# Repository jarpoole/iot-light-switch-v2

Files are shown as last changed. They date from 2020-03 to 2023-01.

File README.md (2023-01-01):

# iot-light-switch-v2

An internet-connected voice-controlled easy-to-use lightswitch controller.

## Features

1. Voice control through google-assistant.
2. Extremely long battery life. The wall-mounted lightswitcher can achieve a very low energy sleep state while the base station remains connected to the internet waiting for commmands.
3. Tool-less magnetic installation.
4. Compatibility with both rocker and post style switches.
5. USB rechargable Li-ion battery pack.
6. Side-by-side installation thanks to narrow width.
7. Contact activation through subtle physical switch.

## Limitations

1. The low-energy 433Mhz radios I selected are not suitable for this project as they are extremely unreliable and require a complicated software state-machine to service. A better choice would have been something like the `NRF24L01+` which includes automatic retransmission, multicast and an extremely low power consumption in sleep. See [this](https://github.com/jarpoole/NRF24L01_driver) project for more.

2. The `ESP8266` WiFi module is not powerful enough to act as a base station for multiple devices. Its single processing core is mostly preoccupied with handling the networking stack and cannot be blocked by user software for two long without connectivity problems. A more modern SoC like the `ESP32` would have been a much better choice.

## Subsystems

- [Light Switch](#light-switch)
  - [Motherboard](#motherboard)
  - [Daughterboard](#daughterboard)
  - [Actuator](#actuator)
- [Base Station](#light-switch)

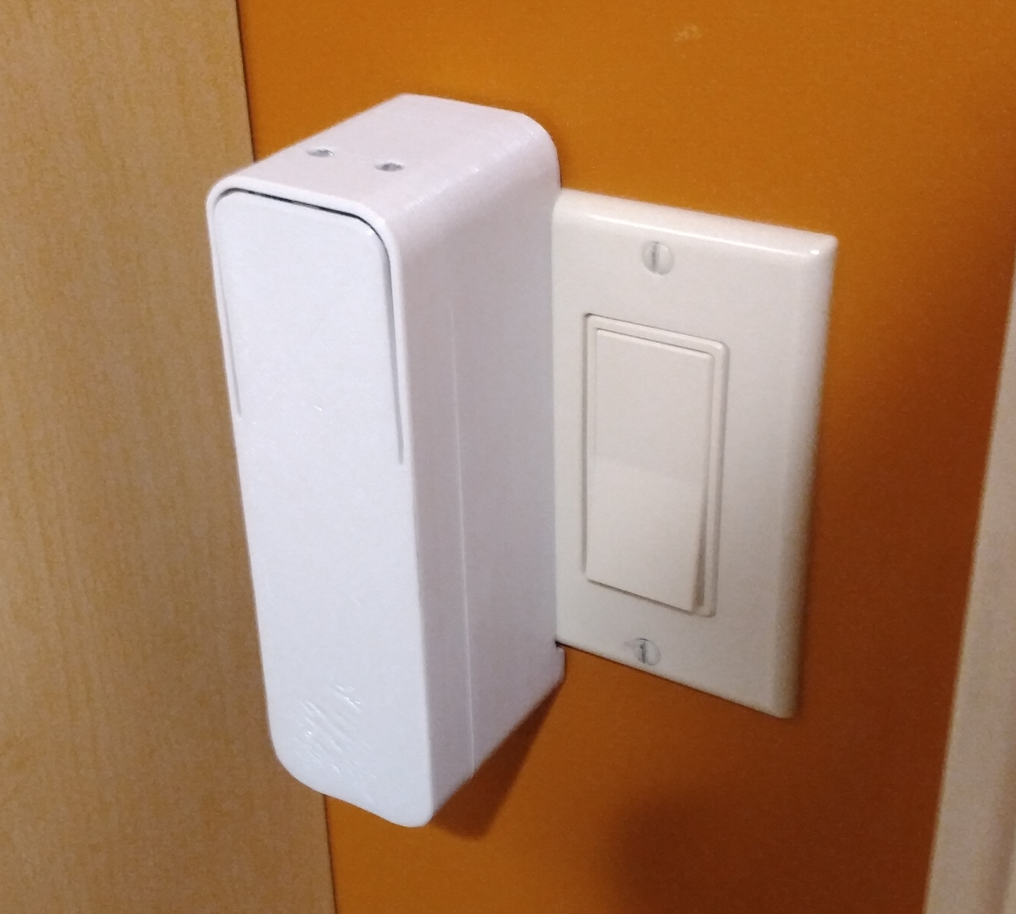
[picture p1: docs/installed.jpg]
installed


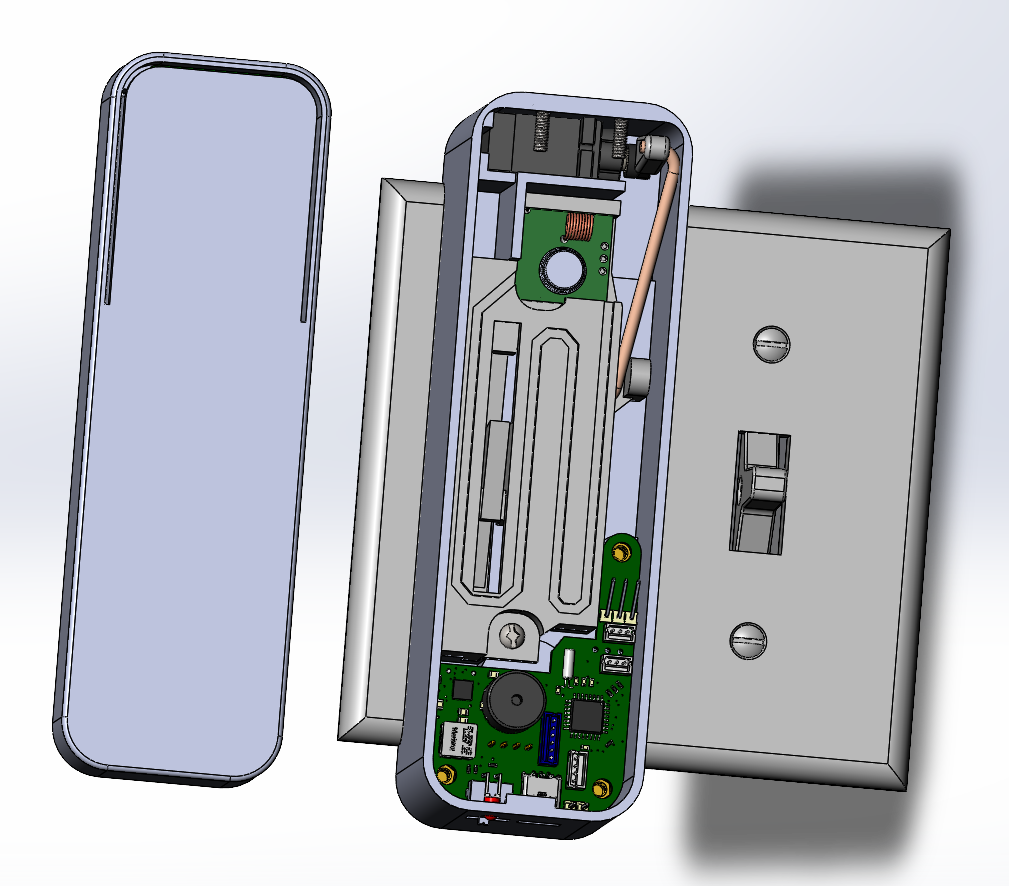
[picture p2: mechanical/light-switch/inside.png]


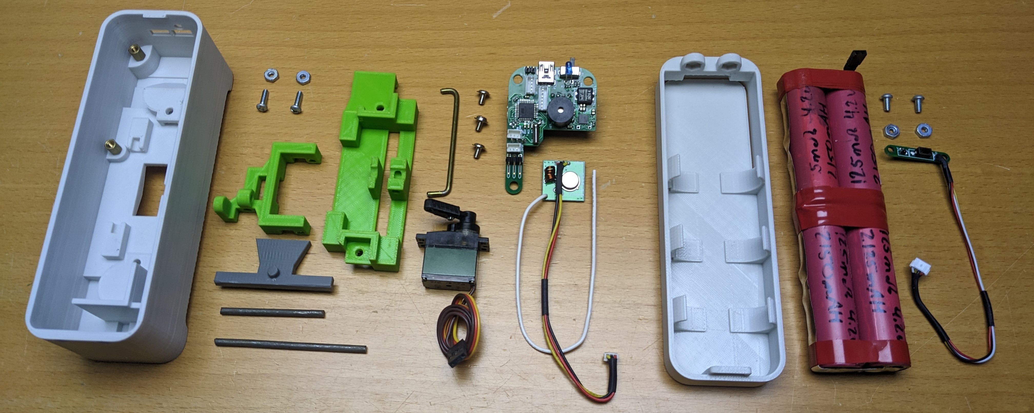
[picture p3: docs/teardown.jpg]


## Light Switch

### Motherboard

1. Low-energy 433Mhz radios
2. Deep-sleep enabled by a 32768Hz oscillator and timer interrupt
3. BMS built around the Texas Instruments BQ25890 buck-boost charge controller. Charges 3.7 Li-ion battery pack from 5v USB power (buck) and produces 5v system power from battery pack when in operation (boost)
4. Audio feedback from a buzzer
5. Integrated USB debug/serial output
6. ICSP programming header

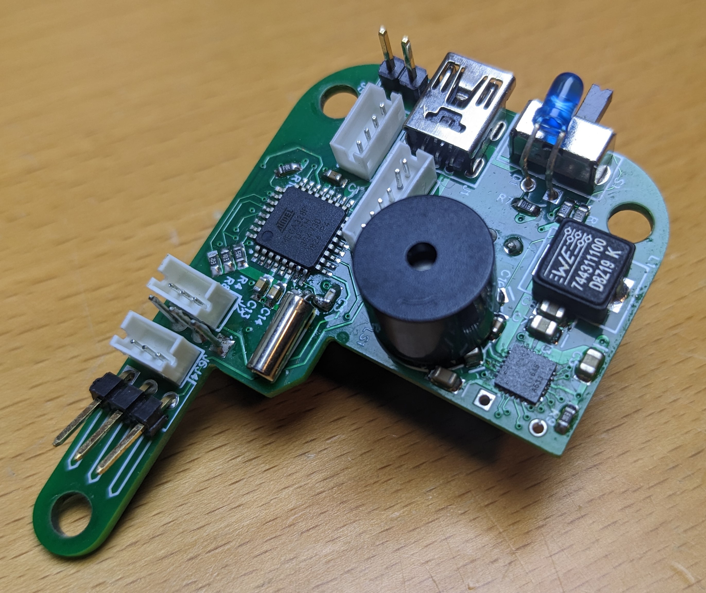
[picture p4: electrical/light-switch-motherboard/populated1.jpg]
motherboard_populated


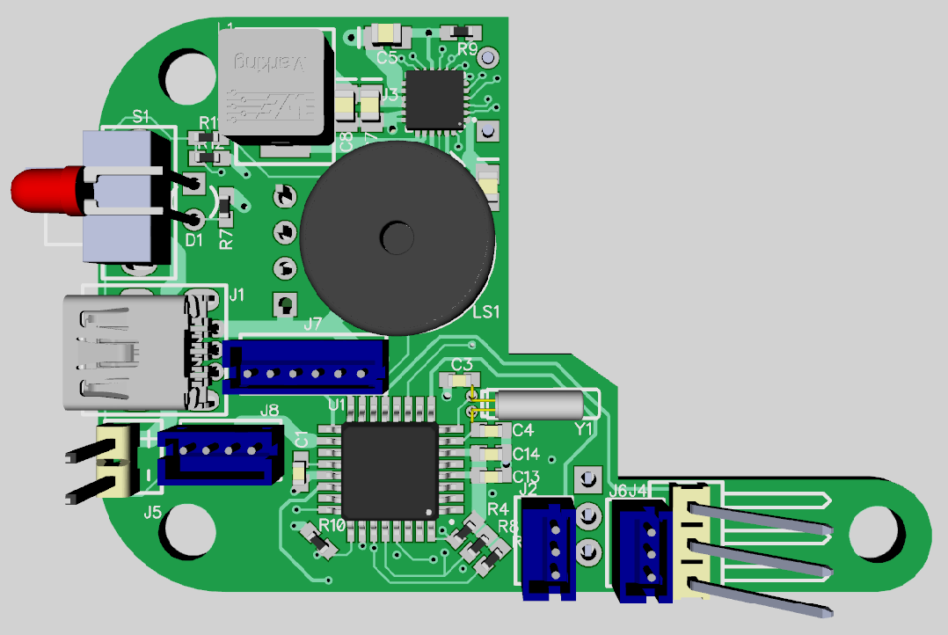
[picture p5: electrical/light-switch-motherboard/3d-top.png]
motherboard_3d_top


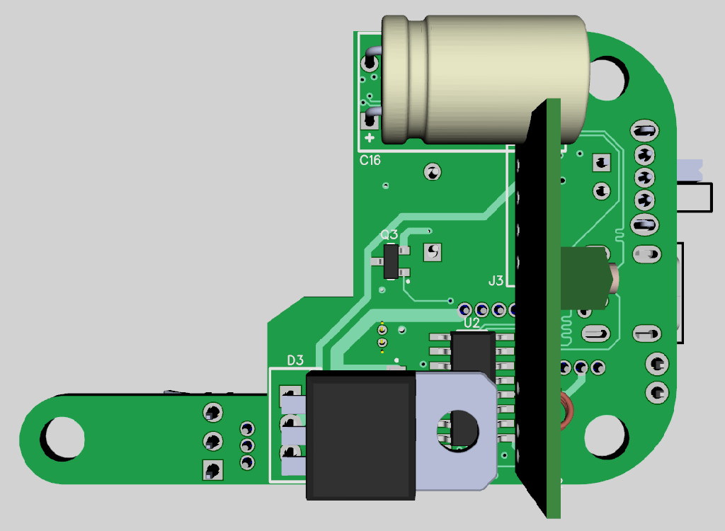
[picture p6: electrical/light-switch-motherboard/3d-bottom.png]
motherboard_3d_bottom


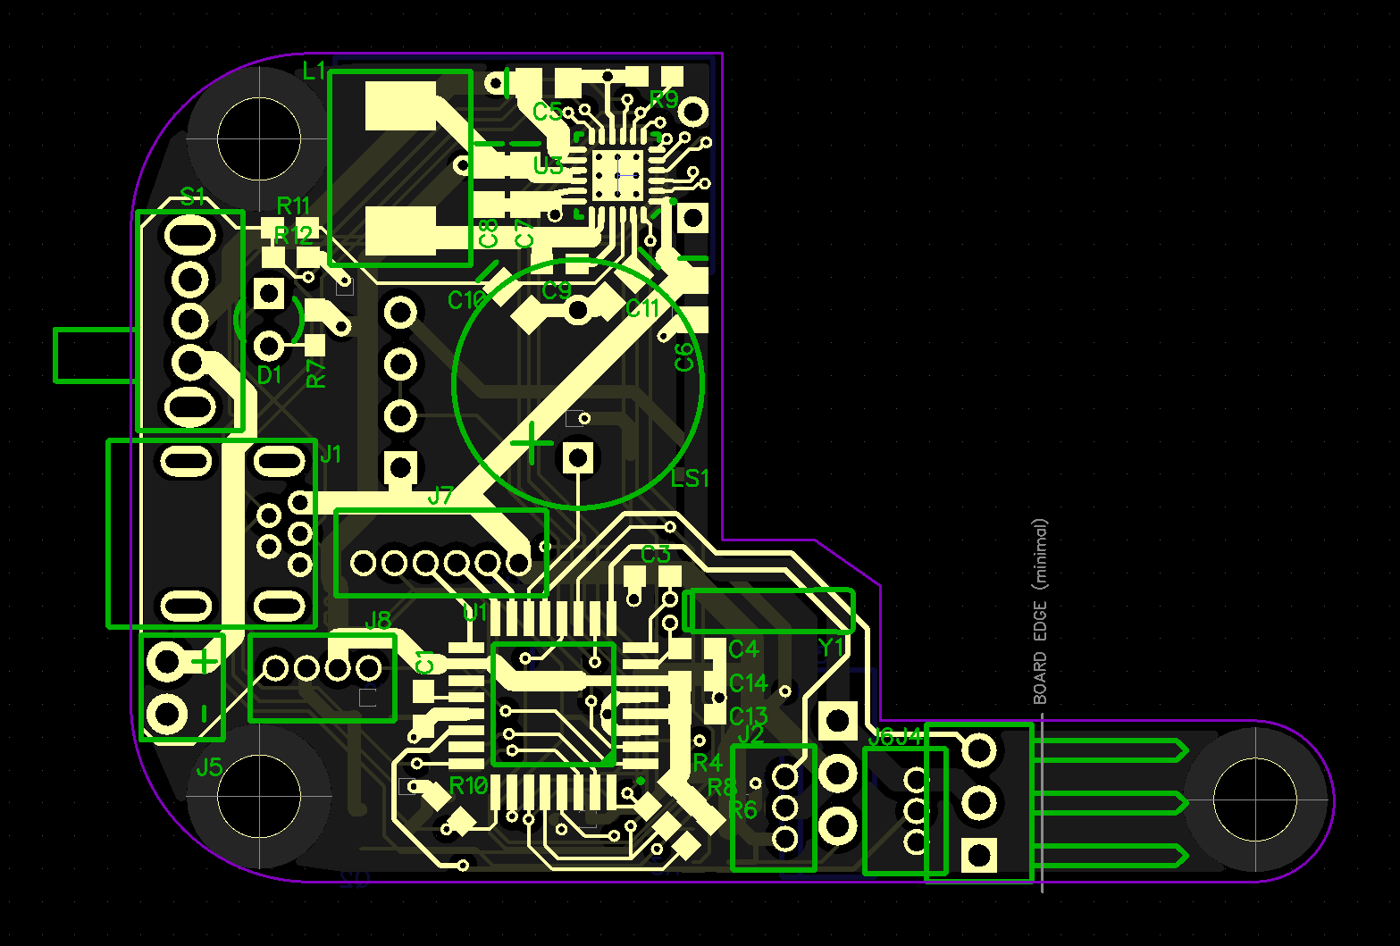
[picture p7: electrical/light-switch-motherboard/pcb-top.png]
motherboard_pcb_top


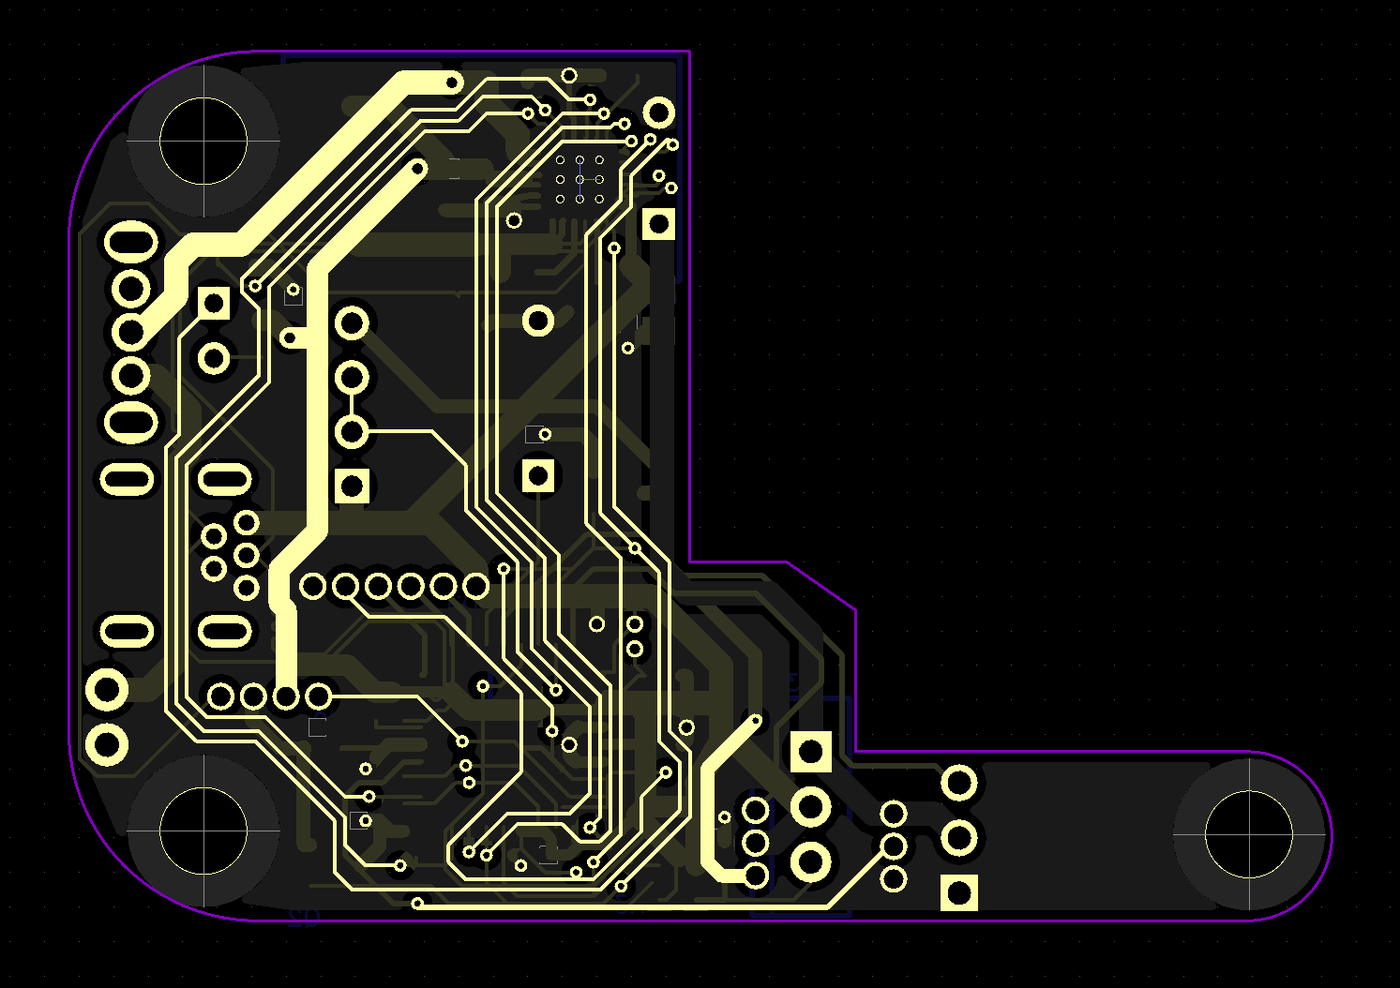
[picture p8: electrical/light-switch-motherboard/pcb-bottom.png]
motherboard_pcb_bottom


### Daughterboard

The daughterboard has two roles

1. To connect a small momentary switch for the front bumper to the motherboard
2. To connect the battery temperature monitoring thermocouple to the motherboard

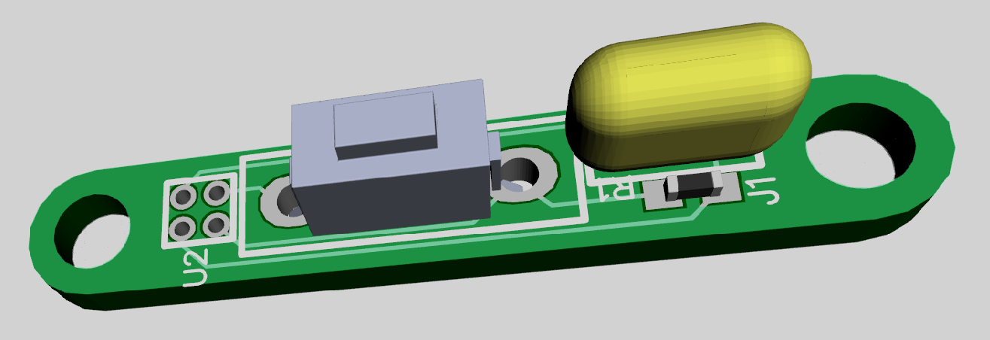
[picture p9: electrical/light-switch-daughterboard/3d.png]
daughterboard_3d


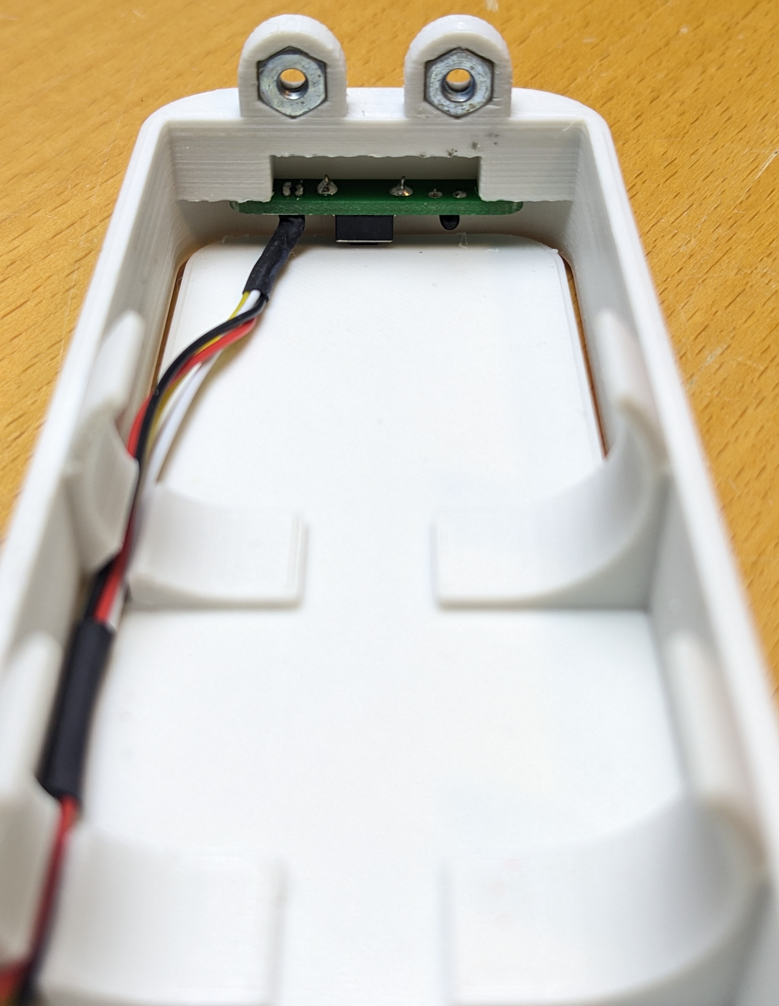
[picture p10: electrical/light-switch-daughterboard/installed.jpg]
daughterboard_installed


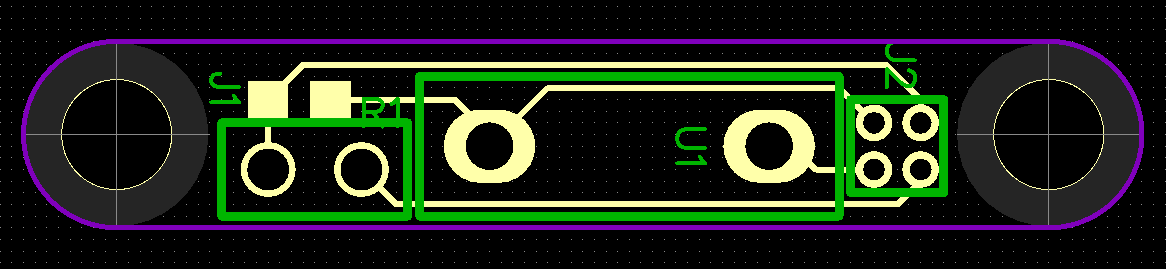
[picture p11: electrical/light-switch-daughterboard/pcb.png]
daughterboard_pcb


### Actuator

The actuator is compatible with both post-style and rocker-style switches. The slide engages with post-style while the vertial rocker engages the rocker-style.

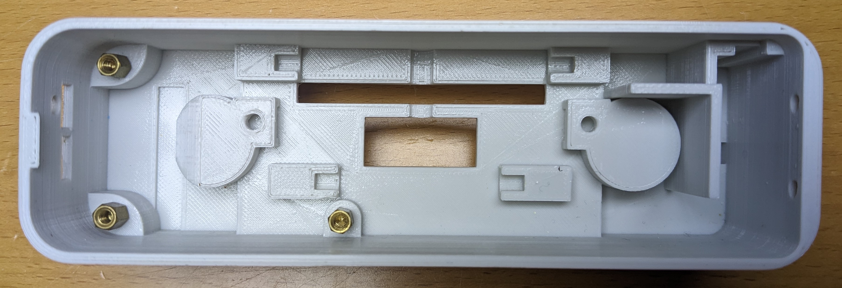
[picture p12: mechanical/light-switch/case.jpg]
case


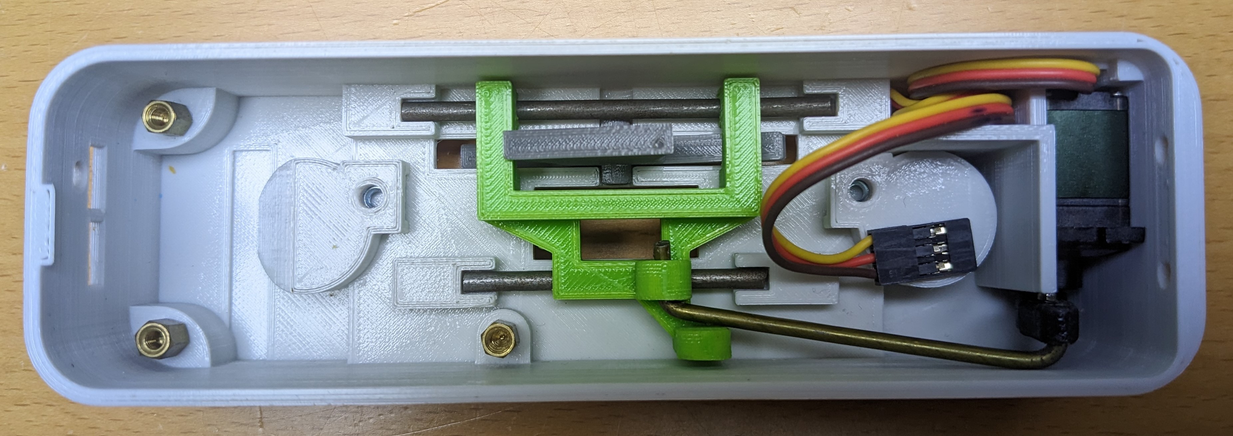
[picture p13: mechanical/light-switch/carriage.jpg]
carriage


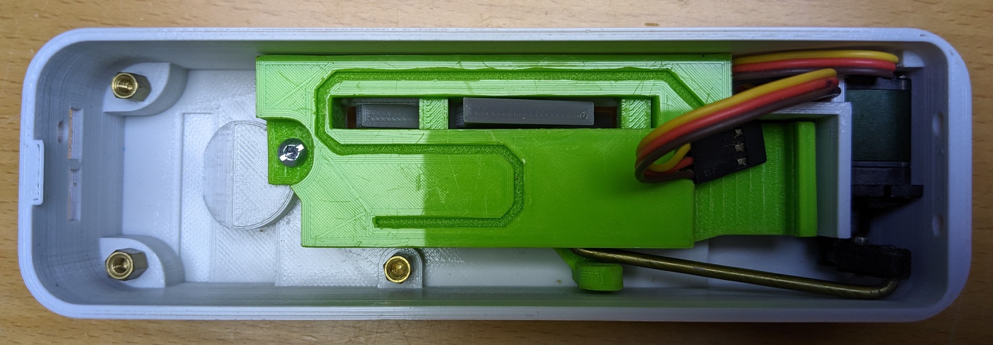
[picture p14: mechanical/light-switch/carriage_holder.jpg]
carriage_holder


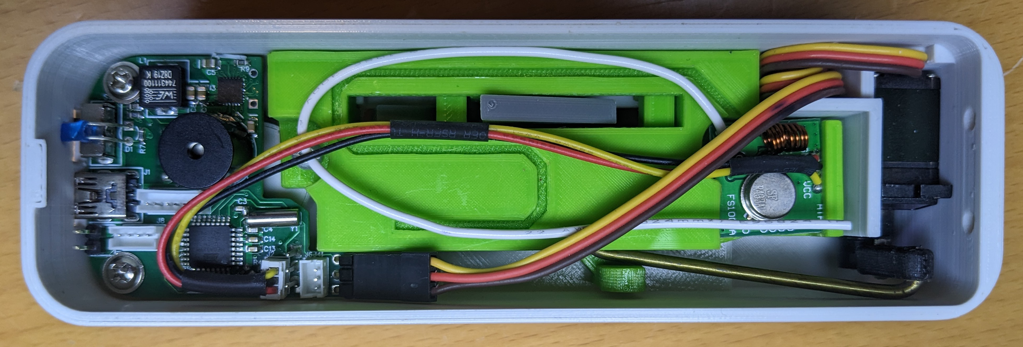
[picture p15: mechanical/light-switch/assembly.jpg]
assembled


## Base Station

The base station's primary responsibility is to act as a bridge between the internet and the low-energy 433Mhz radio on the light-switch.

1. WiFi connectivity using ESP8266
2. Dual power-supply options
   - Mini USB
   - Terminal block 5V DC
3. Integrated USB debug/serial output
4. Captive portal configuration through a mobile browser

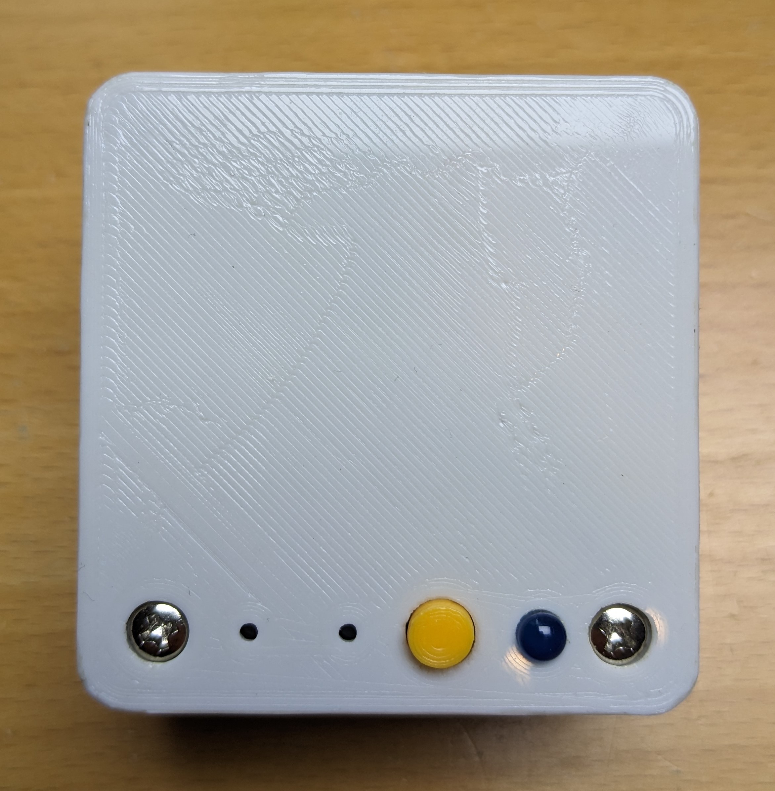
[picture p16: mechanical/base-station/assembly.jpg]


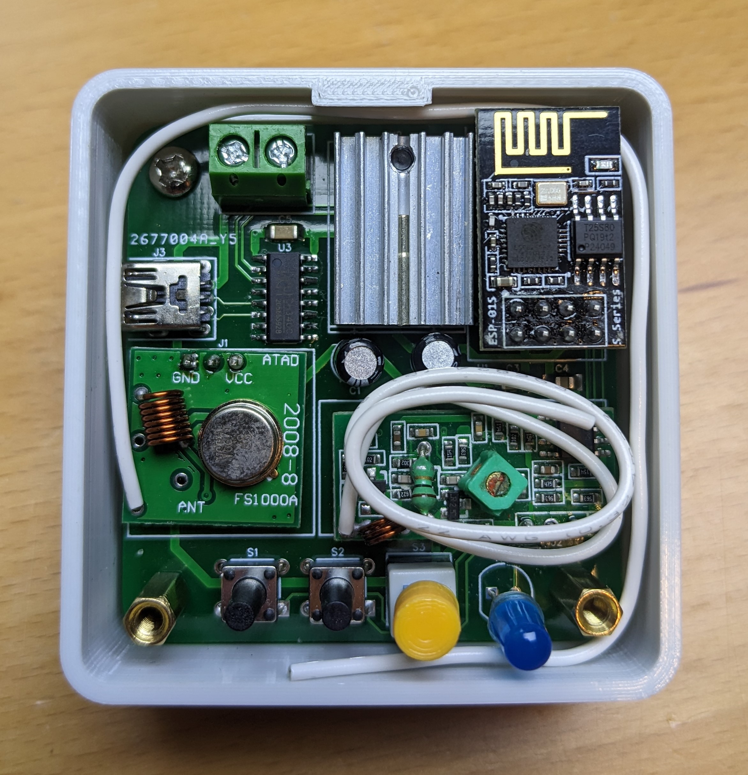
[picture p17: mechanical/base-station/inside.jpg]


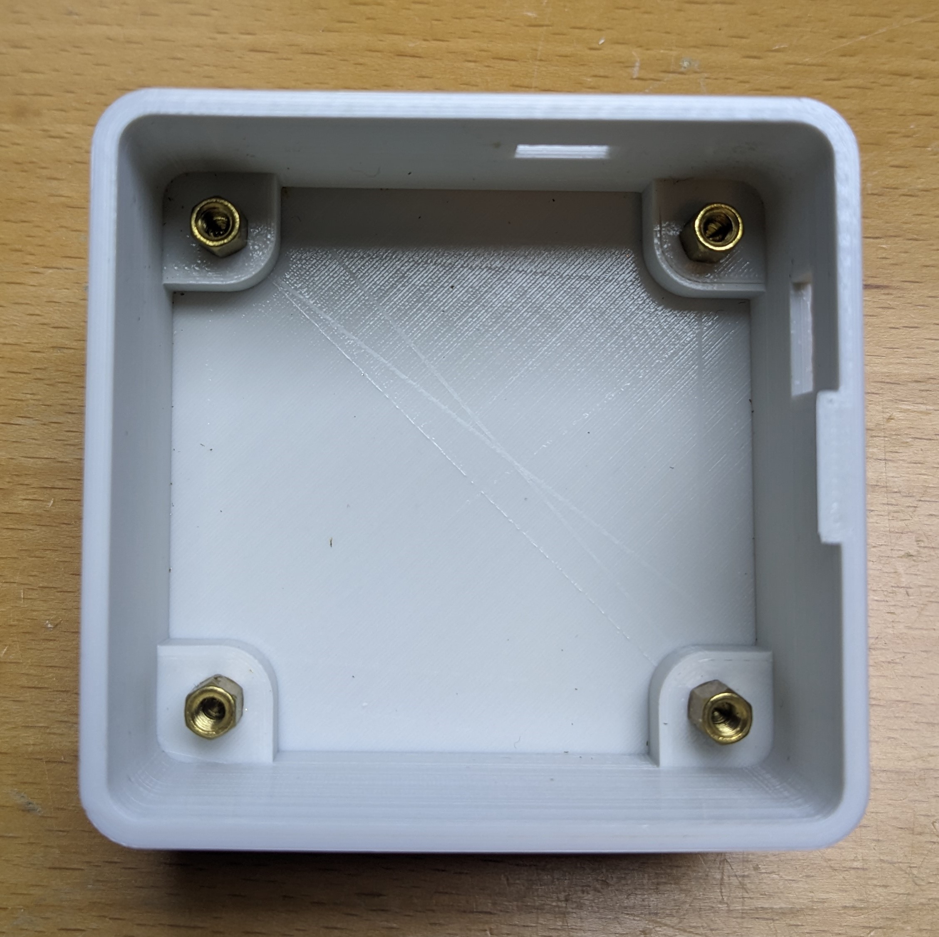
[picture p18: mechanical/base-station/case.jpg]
case


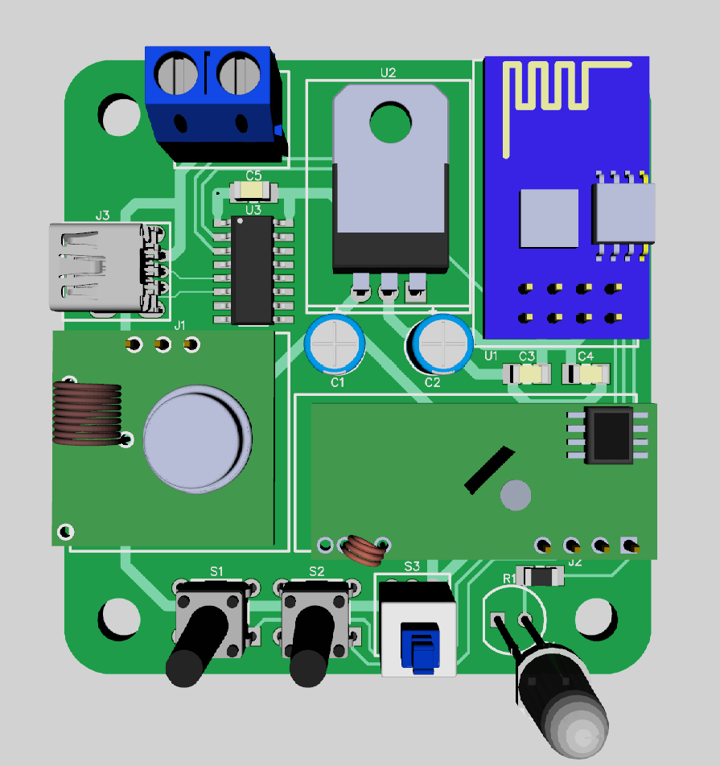
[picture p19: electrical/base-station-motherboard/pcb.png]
base_pcb


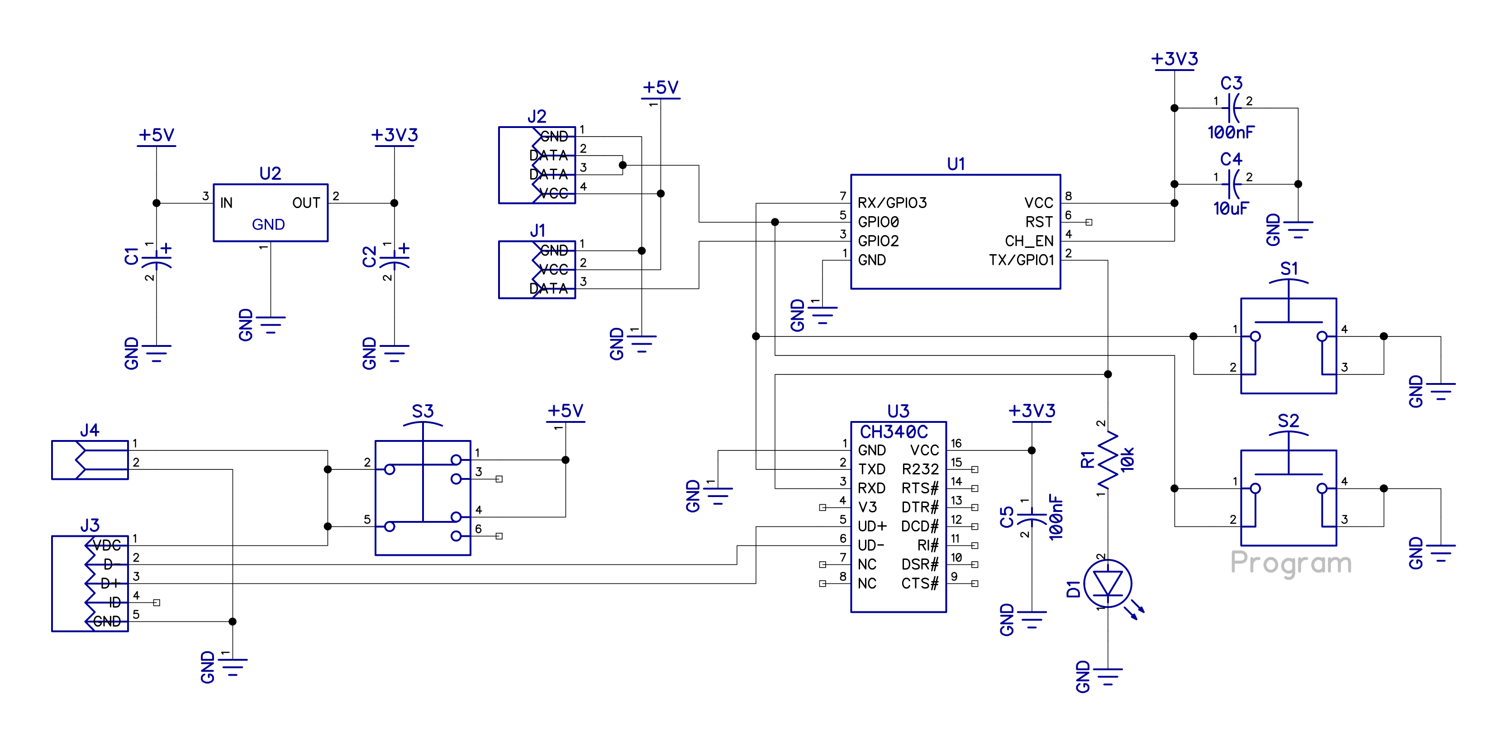
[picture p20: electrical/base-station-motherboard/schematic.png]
schematic


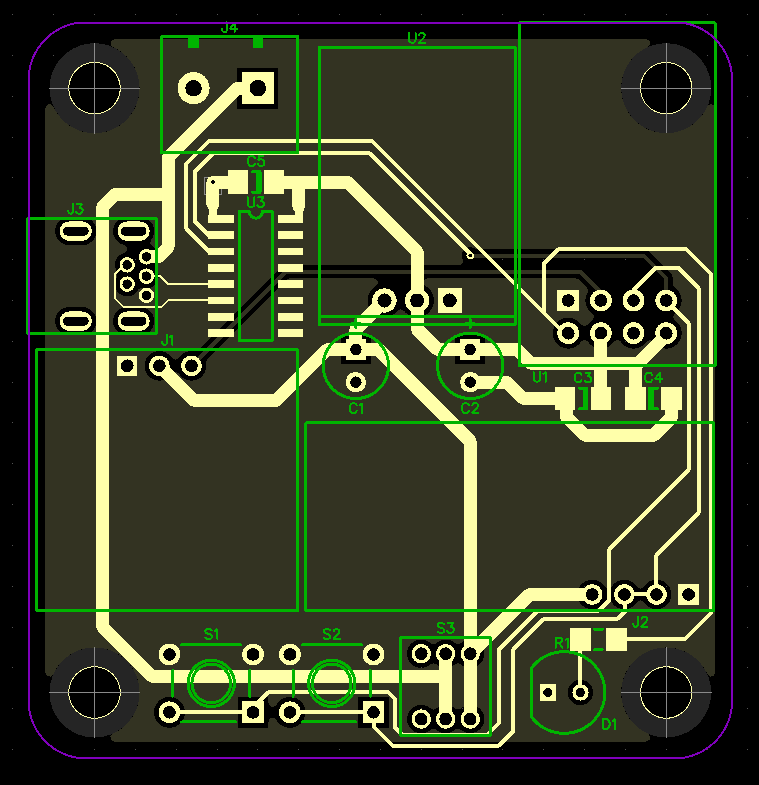
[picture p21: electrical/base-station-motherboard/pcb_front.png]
base_pcb


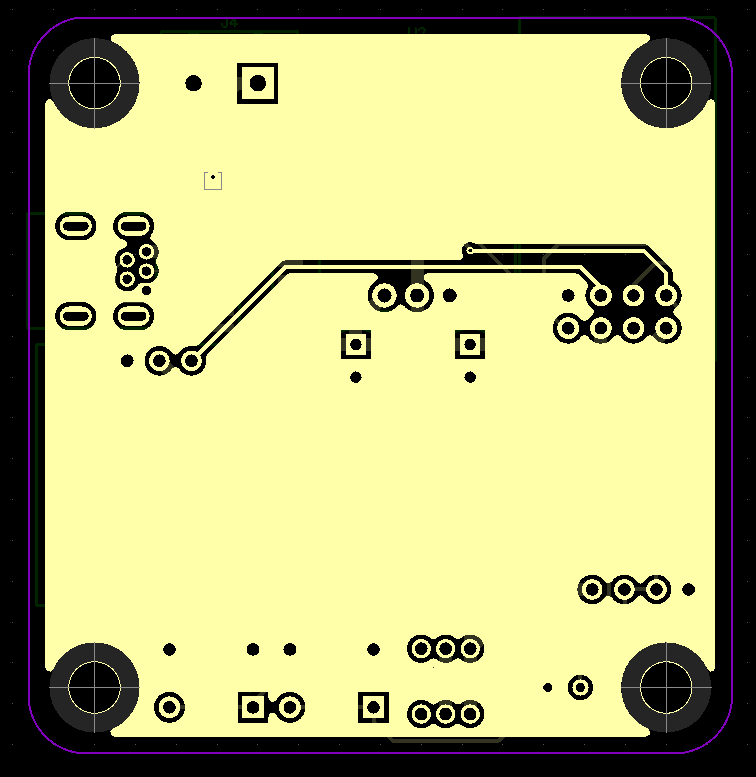
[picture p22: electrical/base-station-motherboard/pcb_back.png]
base_pcb


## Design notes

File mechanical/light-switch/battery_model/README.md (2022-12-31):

# 1s4p 18650 Battery Pack

## Render

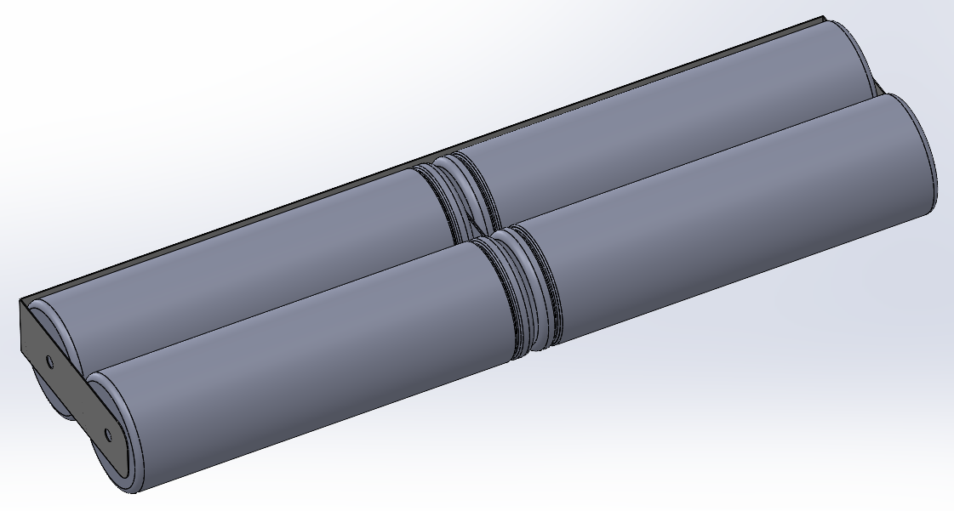
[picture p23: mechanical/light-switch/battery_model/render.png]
render


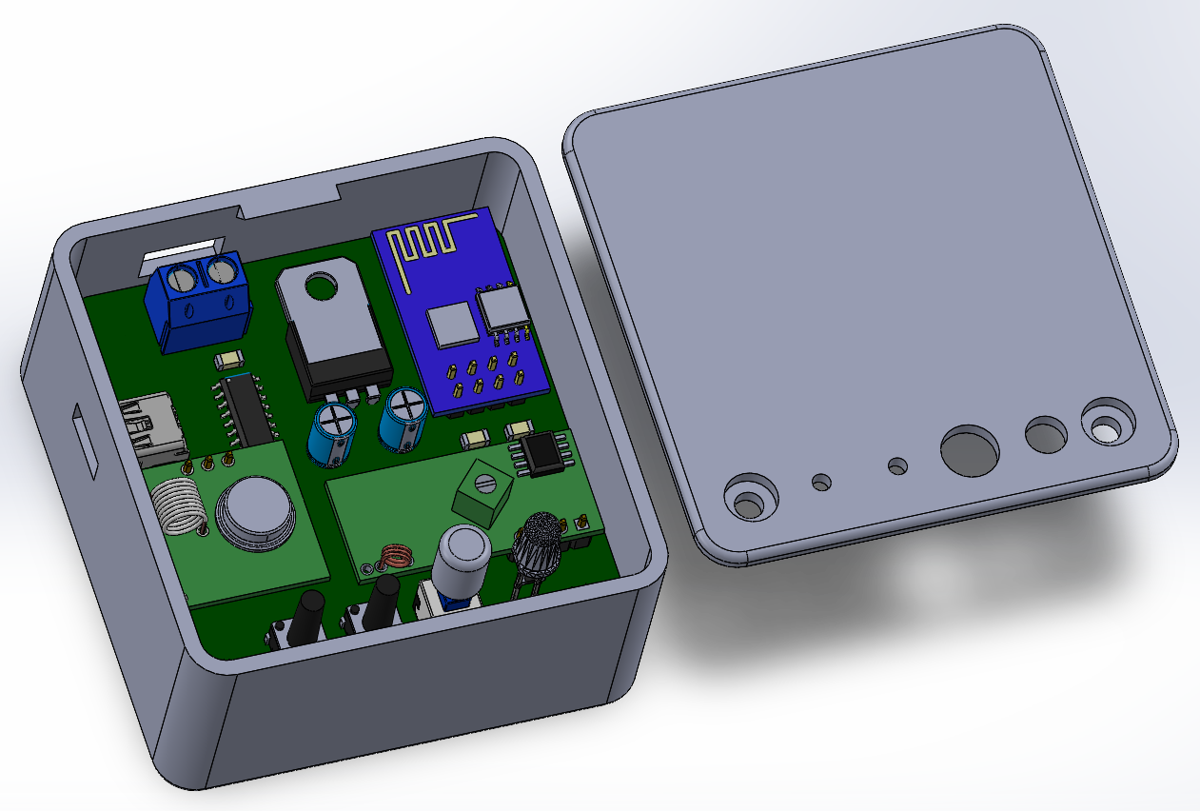
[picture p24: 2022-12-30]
mechanical/base-station/render.png

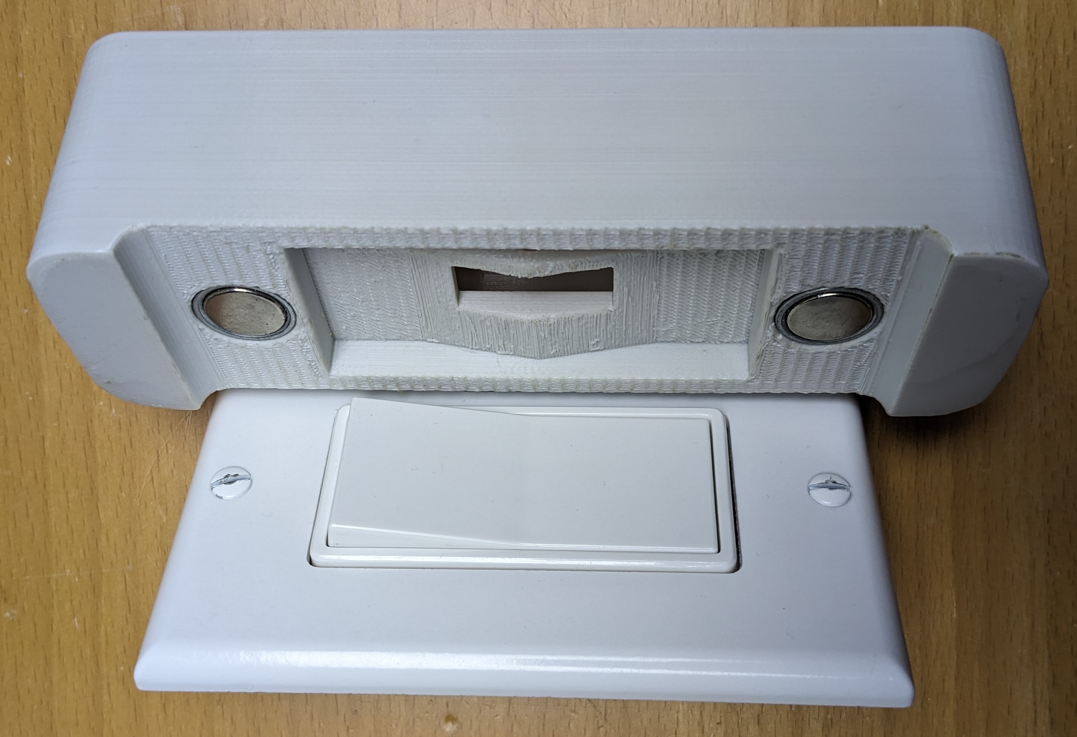
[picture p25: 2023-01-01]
mechanical/light-switch/mount.jpg

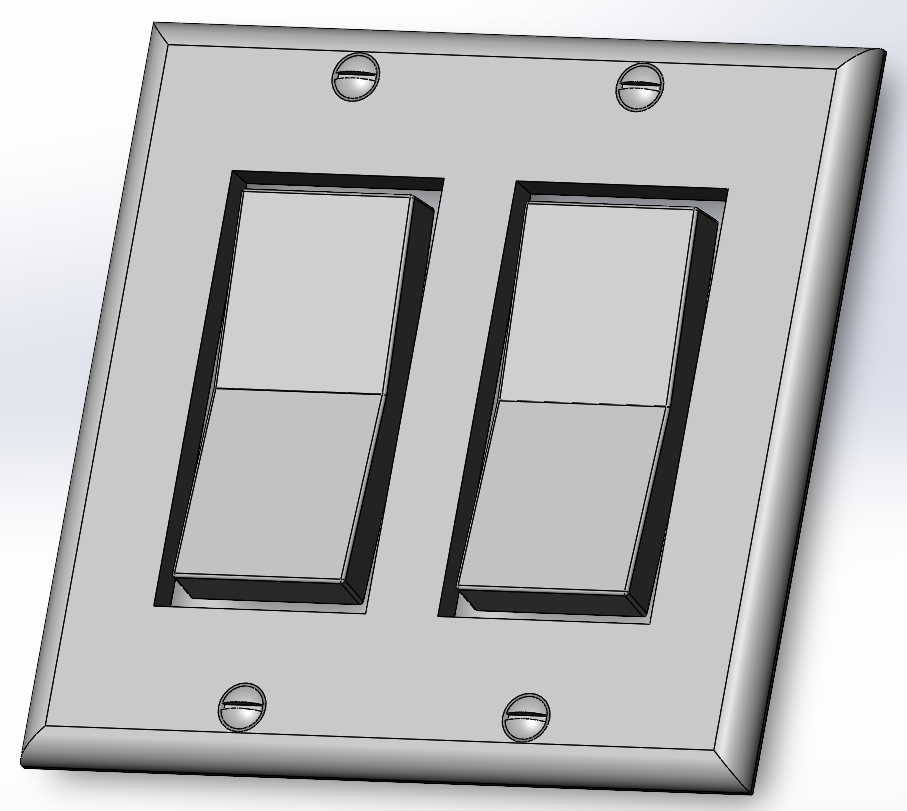
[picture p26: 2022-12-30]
mechanical/light-switch/rocker-switch-model/render.png

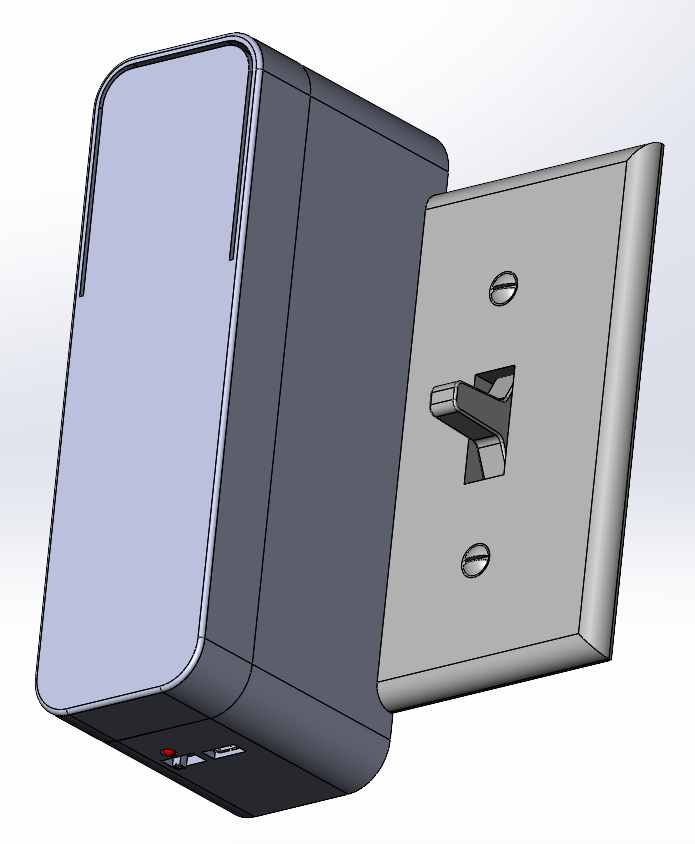
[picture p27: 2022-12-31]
mechanical/light-switch/render.png

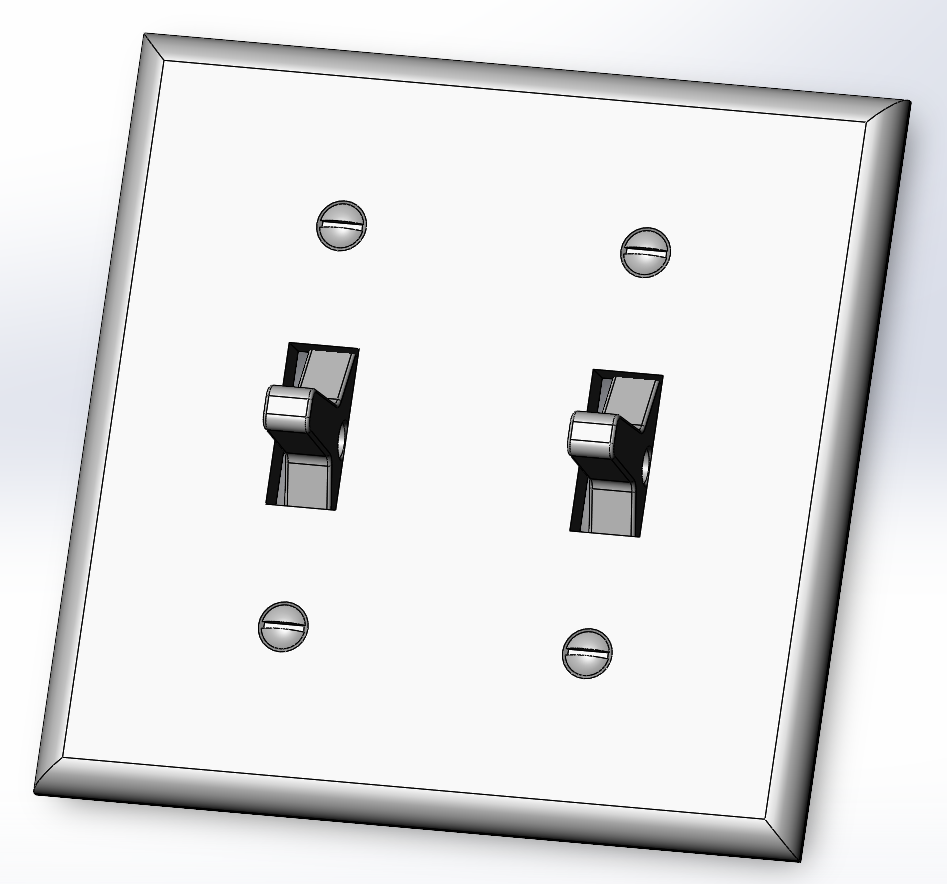
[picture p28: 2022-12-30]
mechanical/light-switch/post-switch-model/render.png

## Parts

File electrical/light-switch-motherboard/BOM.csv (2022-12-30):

Name | Quantity | RefDef | Value
CAP_0603 | 2 | C3, C4 | 18pF
CAP_0603 | 1 | C9 | 47nF
CAP_0603 | 1 | C12 | 10nF
CAP_0603 | 4 | C1, C13, C14, C15 | 100nF
CAP_0805 | 1 | C10 | 4.7uF
CAP_0805 | 4 | C5, C7, C8, C11 | 10uF
CAP_0805 | 1 | C6 | 1uF
CAP Radial Right Angle 10x16x5 | 1 | C16 | 1000uF
LED | 1 | D1 | 3mm blue
1N4148W SOD-123 | 1 | D2
Mini USB Throughole | 1 | J1
RF Reciever connection | 1 | J3
3 pin 2.54mm Right Angle Term Block | 1 | J4
Li-ion CON | 1 | J5
JST ZH 6 Pin | 2 | J7
JST ZH 4 Pin | 2 | J8
JST ZH 3 Pin | 1 | J2, J6
PA4333.102NLT? Inductor | 1 | L1 | 1uH, 8.7mR
PB-1224PE-05Q | 1 | LS1
IRL540 | 1 | Q1
2N7002 N-Channel MOSFET | 2 | Q2, Q3
RES_0603 | 8 | R1, R2, R4, R5, R6, R8, R9, R10 | 10k
RES_0603 | 1 | R7 | 1k
RES_0603 | 1 | R3 | 220R
RES_0603 | 1 | R11 | 5.23k
RES_0603 | 1 | R12 | 28.7k
SPDT switch | 1 | SW1
ATMEGA328_TQFP32 | 1 | U1
CH340G (SOP) | 1 | U2
BQ25890 | 1 | U3
TC26H | 1 | Y1 | 32.768KHz

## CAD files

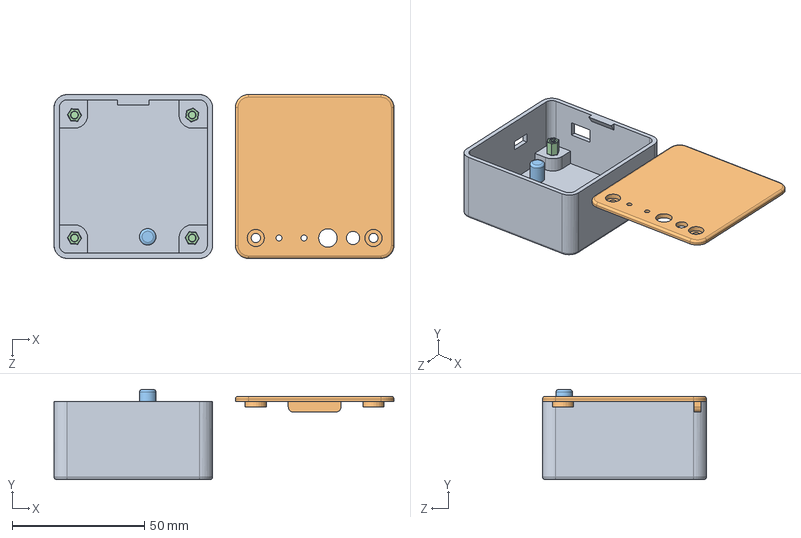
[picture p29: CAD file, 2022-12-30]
mechanical/base-station/assembly.SLDASM
128.6 x 34.1 x 62.0 mm
Bottom case
lid
button
6+6 M3 Standoff x 4

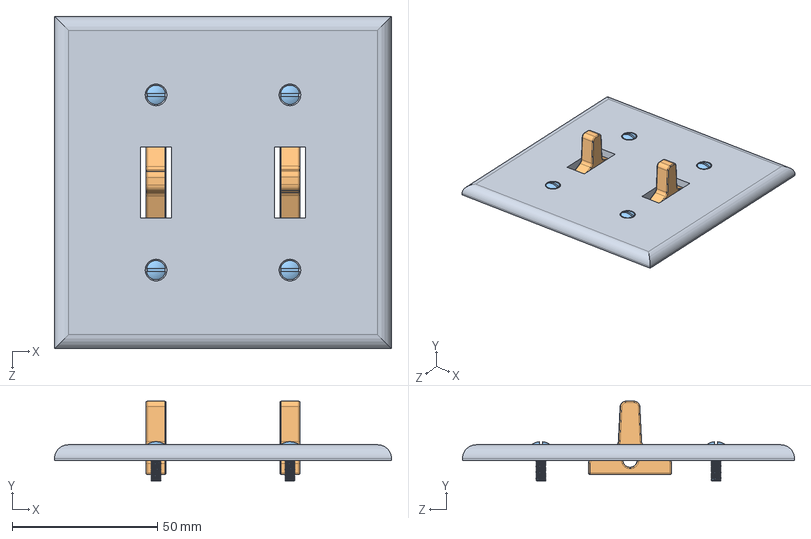
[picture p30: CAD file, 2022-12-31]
mechanical/light-switch/post-switch-model/post-switch.SLDASM
116.0 x 27.4 x 114.3 mm
switchplate
post x 2
screw x 4

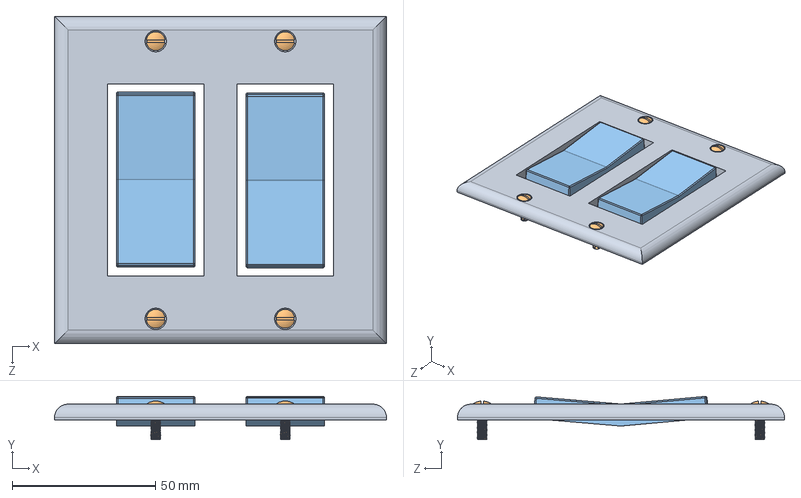
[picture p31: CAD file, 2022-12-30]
mechanical/light-switch/rocker-switch-model/rocker-switch.SLDASM
116.0 x 15.1 x 114.3 mm
switchplate
screw x 4
rocker x 2

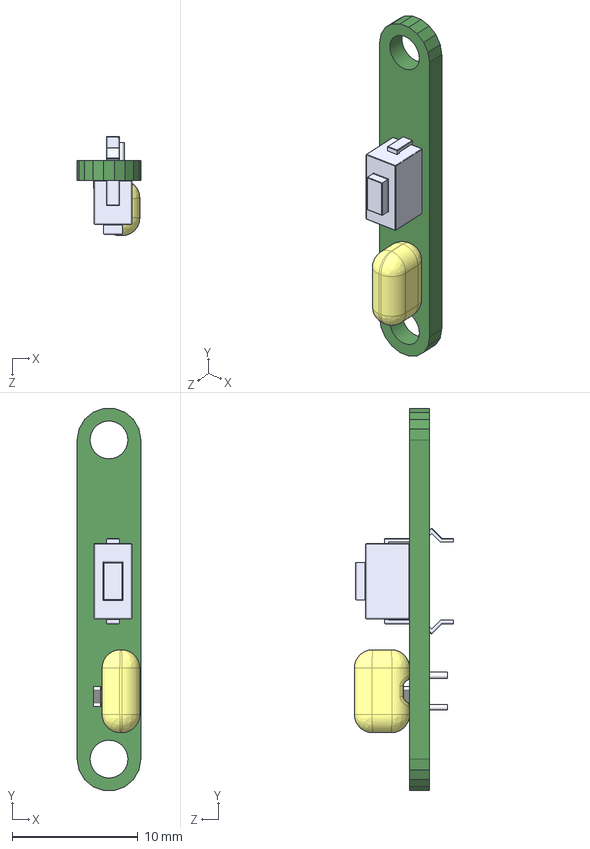
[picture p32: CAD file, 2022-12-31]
electrical/light-switch-daughterboard/3d.step
5.08 x 30.4 x 7.90 mm
Board_3d
cap-2.54_6.6x3
res_0603
3x6x4.3mm_Button

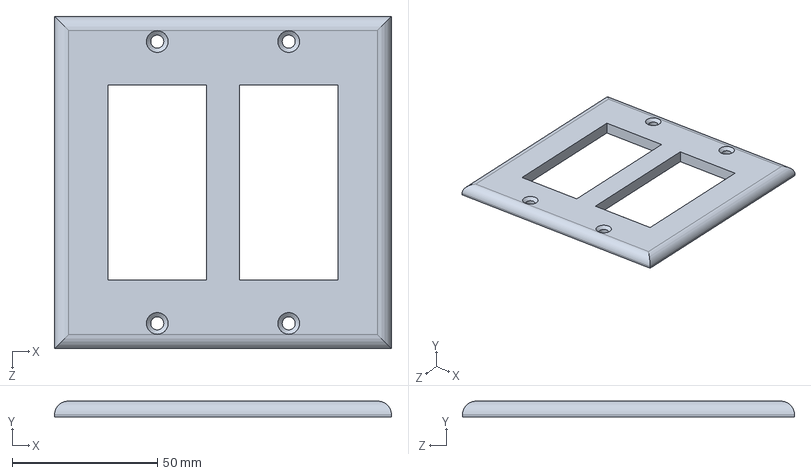
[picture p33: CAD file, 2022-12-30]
mechanical/light-switch/rocker-switch-model/switchplate.SLDPRT
116.0 x 5.50 x 114.3 mm

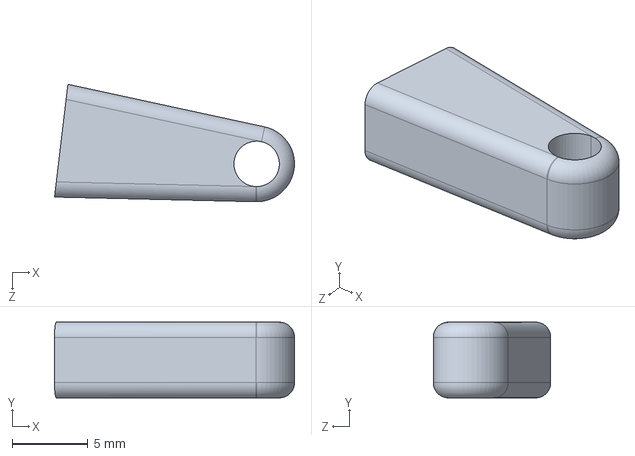
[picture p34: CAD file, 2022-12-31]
mechanical/light-switch/servo_horn_extender.STEP
15.9 x 5.00 x 7.76 mm

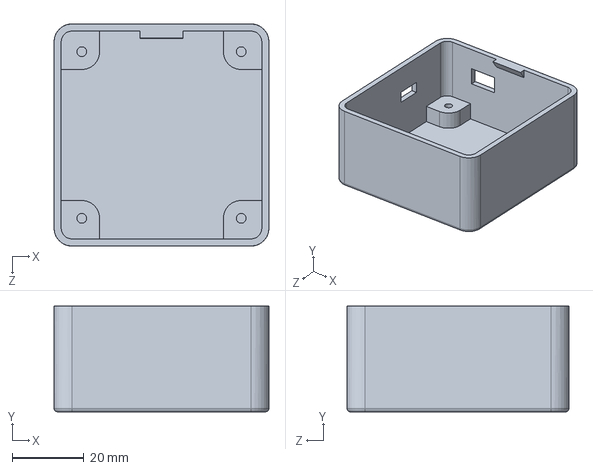
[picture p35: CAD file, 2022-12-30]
mechanical/base-station/case.SLDPRT
60.0 x 29.5 x 62.0 mm

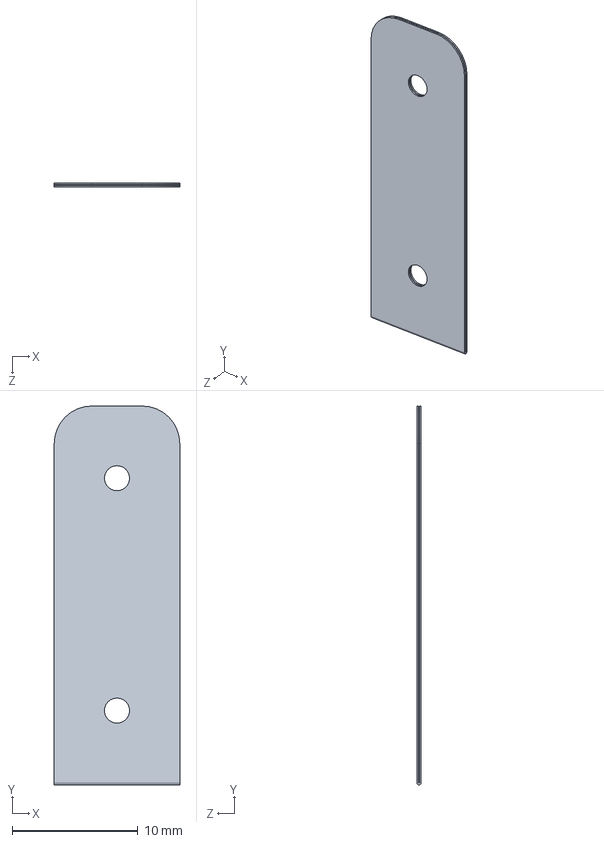
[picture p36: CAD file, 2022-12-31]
mechanical/light-switch/battery_model/1s4p_battery_inner_tab.SLDPRT
10.0 x 30.2 x 0.35 mm

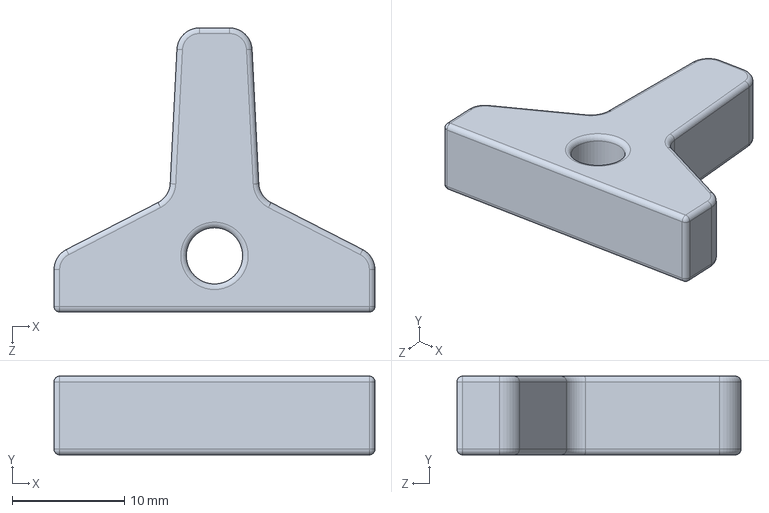
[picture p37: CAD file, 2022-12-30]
mechanical/light-switch/post-switch-model/post.SLDPRT
28.5 x 7.00 x 25.3 mm

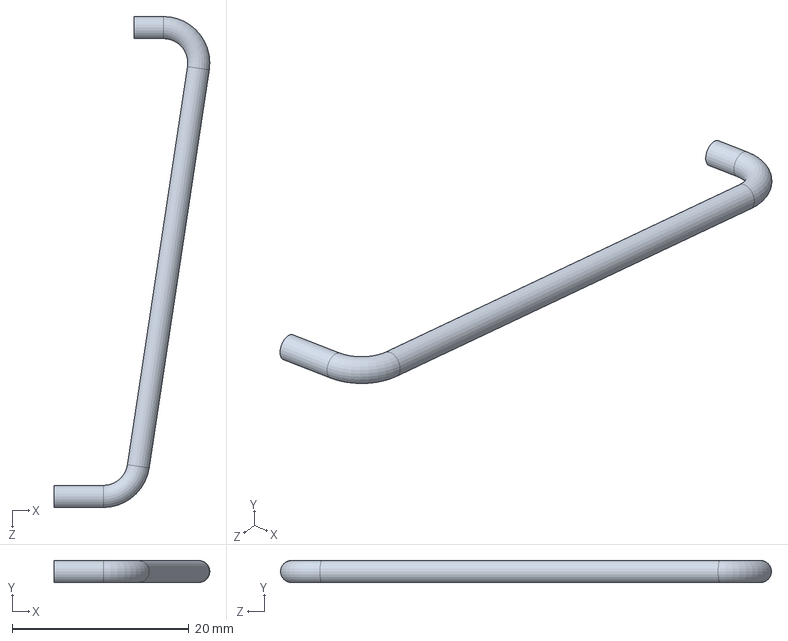
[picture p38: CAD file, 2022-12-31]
mechanical/light-switch/servo_lever_arm.SLDPRT
17.6 x 2.50 x 55.5 mm

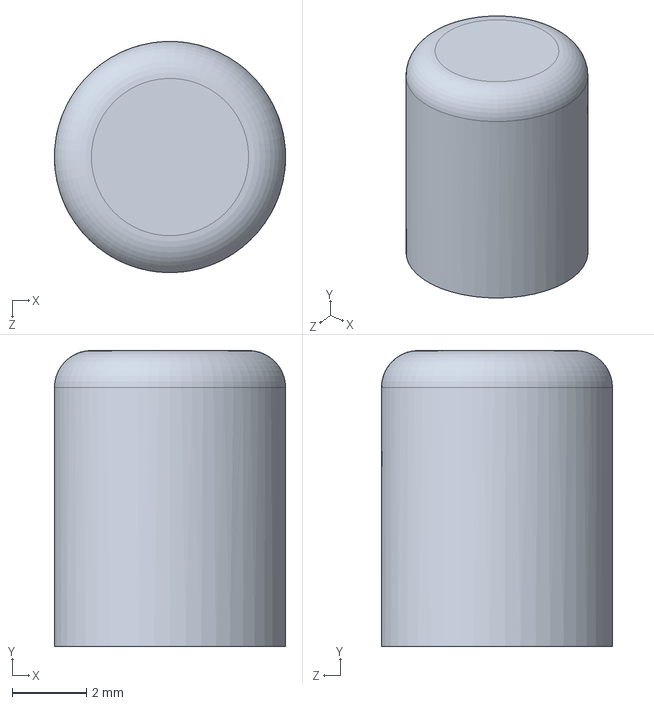
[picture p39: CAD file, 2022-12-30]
mechanical/base-station/button.SLDPRT
6.25 x 8.00 x 6.25 mm

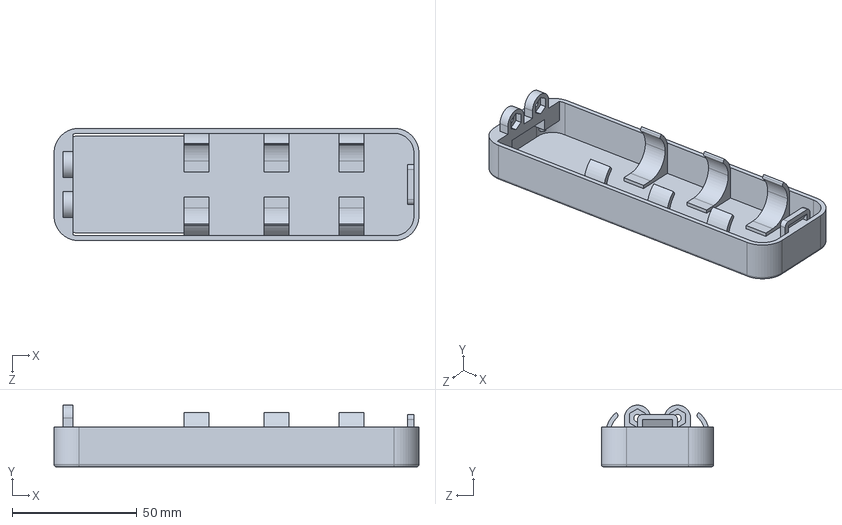
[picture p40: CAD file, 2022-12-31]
mechanical/light-switch/battery_holder.STEP
146.0 x 24.8 x 45.0 mm

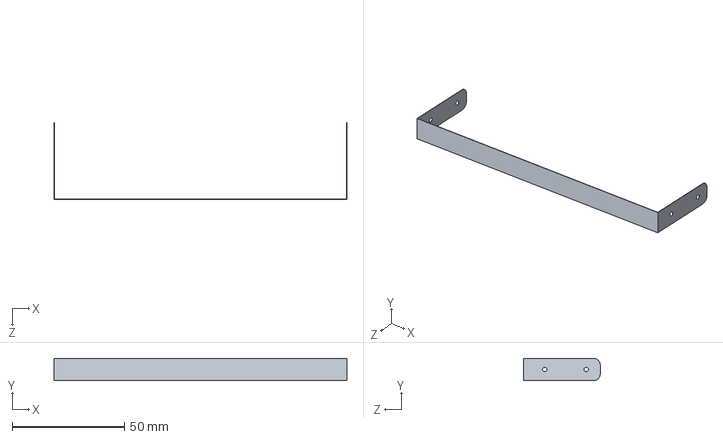
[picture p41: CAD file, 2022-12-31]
mechanical/light-switch/battery_model/1s4p_battery_outer_tab.SLDPRT
130.6 x 10.0 x 34.2 mm

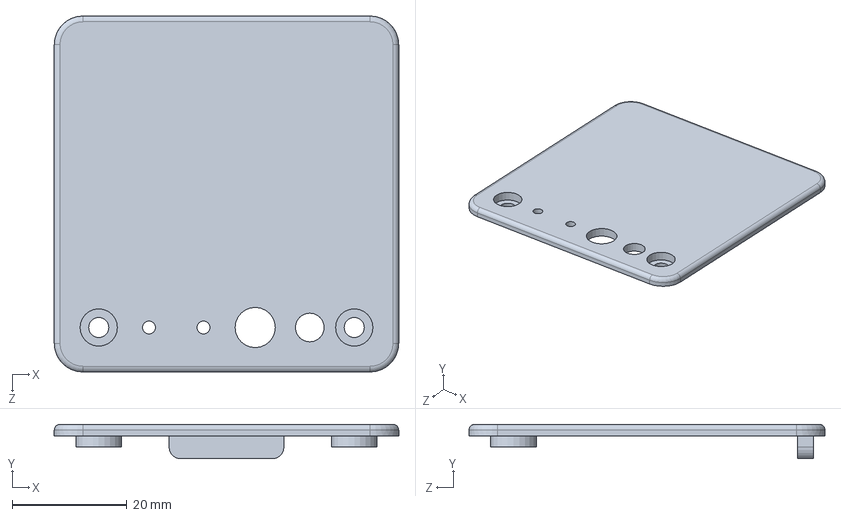
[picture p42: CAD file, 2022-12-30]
mechanical/base-station/lid.SLDPRT
60.0 x 6.00 x 62.0 mm

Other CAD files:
mechanical/light-switch/battery_model/1s4p_battery_pack.SLDASM
mechanical/light-switch/post-switch-model/switchplate.SLDPRT
mechanical/light-switch/rocker-switch-model/rocker.SLDPRT
mechanical/light-switch/rocker.STEP
mechanical/base-station/button.STL
mechanical/base-station/case.STL
mechanical/base-station/lid.STL
mechanical/light-switch/battery_holder.SLDPRT
mechanical/light-switch/battery_model/18650_battery.SLDPRT
mechanical/light-switch/carriage.SLDPRT
mechanical/light-switch/carriage.STEP
mechanical/light-switch/carriage_holder.SLDPRT
mechanical/light-switch/carriage_holder.STEP
mechanical/light-switch/case.SLDPRT
mechanical/light-switch/case.STEP
mechanical/light-switch/old/base_v1.STL
mechanical/light-switch/old/base_v2.STL
mechanical/light-switch/old/base_v3.STL
mechanical/light-switch/old/base_v4.STL
mechanical/light-switch/old/base_v5.STL
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

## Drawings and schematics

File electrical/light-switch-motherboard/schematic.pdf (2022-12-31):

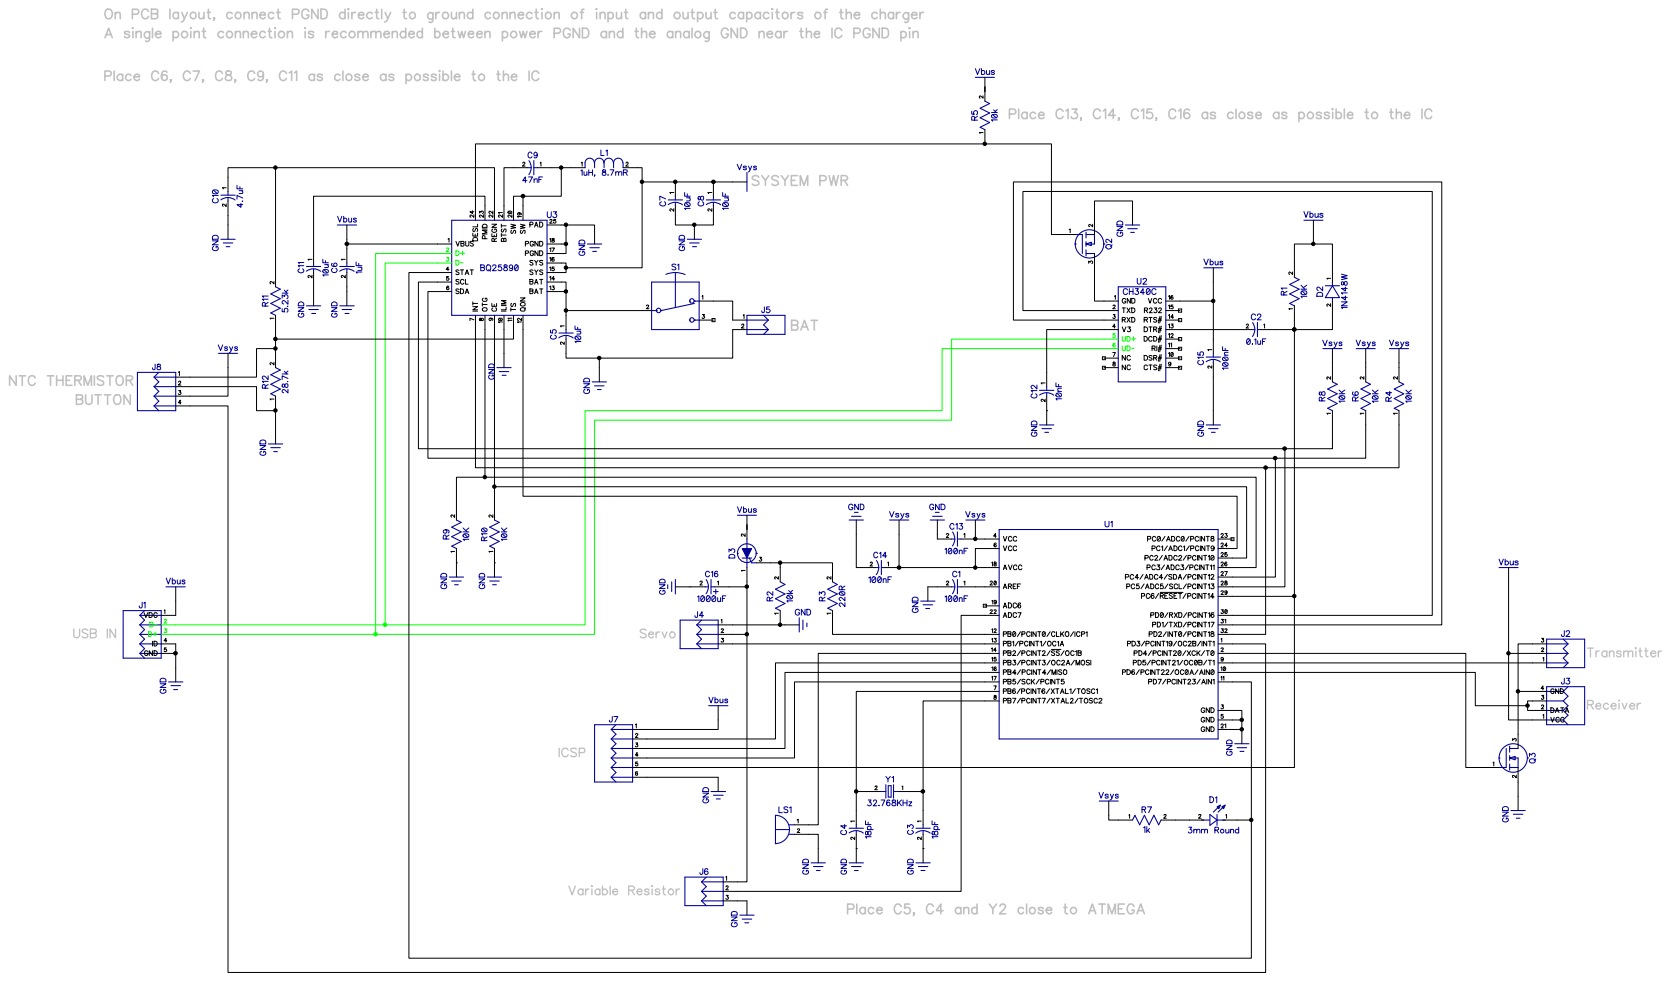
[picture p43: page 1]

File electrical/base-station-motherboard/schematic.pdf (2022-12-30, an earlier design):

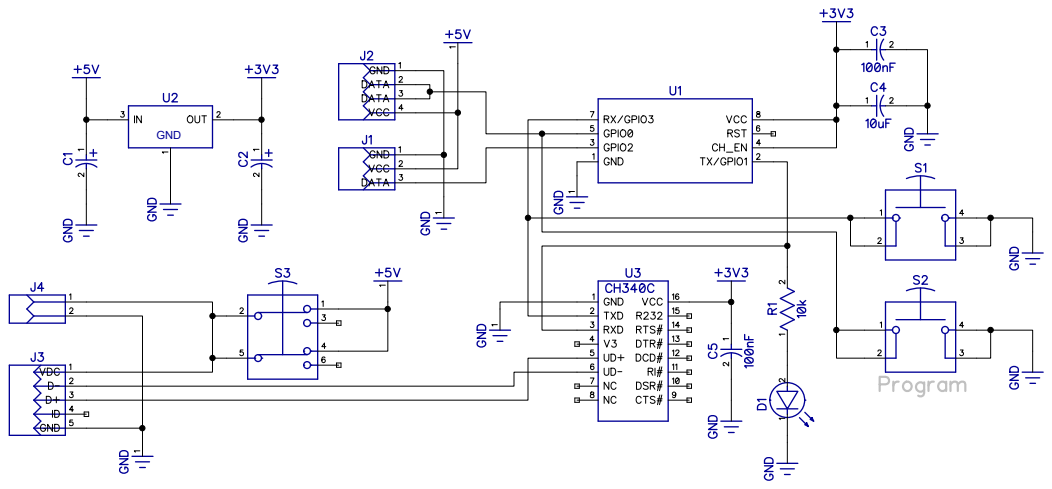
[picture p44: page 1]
GND

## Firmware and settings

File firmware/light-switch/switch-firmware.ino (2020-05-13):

//User files
#include "Constants.h"
#include "BoardV2.h"

//System libraries
#include <avr/io.h>
#include <avr/interrupt.h>
#include <util/delay.h>
#include <avr/sleep.h>
#include <avr/wdt.h>
#include <avr/pgmspace.h>
#include <util/twi.h>

//Modified RadioHead library
#include "./radiohead-ask-atmega328p/RadioHead.h"
#include "./radiohead-ask-atmega328p/RH_ASK.h"
#include "./radiohead-ask-atmega328p/RH_ASK.cpp"
#include "./radiohead-ask-atmega328p/RHCRC.h"
#include "./radiohead-ask-atmega328p/RHCRC.cpp"
#include "./radiohead-ask-atmega328p/RHGenericDriver.cpp"
#include "./radiohead-ask-atmega328p/RHGenericDriver.h"

#include "./pwmservo-atmega328p/PWMServo.h"
#include "./pwmservo-atmega328p/PWMServo.cpp"

//From documentation: RH_ASK (uint16_t speed=2000, uint8_t rxPin=11, uint8_t txPin=12, uint8_t pttPin=10, bool pttInverted=false)
//pttPin = -1 will disable push to talk functionality
RH_ASK ask_driver = RH_ASK(500, RECEIVER, TRANSMITTER, -1, false);

PWMServo servo;

volatile long lastButtonPressedTime = 0;
volatile bool lastButtonState = false;

volatile bool switchOn = false;
volatile bool debugOn = false;           

//ISR Toggles
volatile bool requestSwitchOn = false;
volatile bool requestSwitchOff = false;
volatile bool requestSwitchToggle = false;
volatile bool requestEnableSerial = false;
volatile bool requestDisableSerial = false;

volatile bool requestBeep = false;
volatile byte numBeeps = 0;
volatile bool requestNewPollRate = false;
volatile byte pollRate = 0;

int main (void){
  beep(1,10);
  initialize();
  beep(5,10);

  digitalWrite(BMS_OTG, HIGH);
  while(true){

    digitalWrite(BMS_OTG, HIGH); //enable boost mode
    //serialWriteString("Awake\n");
    //printAllREG();
    processISRUpdates();                //Check for changes generated by the ISR

    
    byte buf[6] = {0xFF,0xFF,0xFF,0xFF,0xFF,0xFF};
    //byte buf[6];
    byte len = sizeof(buf);
    receiveASKBytes(buf, &len);  //blocking
    _delay_ms(10);
    
    transmitASKByte(ACK);
    transmitASKByte(ACK);
    transmitASKByte(ACK);

    
    //for(int i = 0; i < len; i++){
    //  serialWriteString(integerToHex(buf[i]));
    //  serialWriteString(" ");
    //}
    //serialWriteString("\n");
    
   
    processASKCommands(buf,len);             
    processISRUpdates();                //Check for changes generated by the ISR
   
    //serialWriteString("Asleep\n");
    digitalWrite(BMS_OTG, LOW); //disable boost mode
    beep(2,10);
    _delay_ms(50);
    sleep();
    
    /*
    PORTD |= 0b00100000; 
    _delay_ms(2);
    PORTD &= 0b11011111; 
    _delay_ms(2);
    */
    
  }
}

void initialize() {
  //_delay_ms(500);
  
  MCUSR &= ~(1<<WDRF); //Always clear the watchdog system reset flag on startup, p45
  WDTCSR &= ~(1<<WDE); //Always clear the watchdog system reset mode on startup, p45
  
  //----------------------Initialize IO-------------------------
  pinMode(BUZZER, OUTPUT);
  pinMode(BUTTON, INPUT);
  pinMode(LED, INPUT);
  attachInterrupt(digitalPinToInterrupt(BUTTON), buttonISR, RISING);
 
  //enableSerial();                      //---------------------FIX ME Should be disabled by default---------------------
  
  pinMode(SERVO_ENABLE, OUTPUT);
  digitalWrite(SERVO_ENABLE, LOW);

  //---------------------Initialize Radio------------------------
  pinMode(TRANSMITTER, OUTPUT);
  pinMode(RECEIVER, INPUT);
  pinMode(RF_ENABLE, OUTPUT);           
  //digitalWrite(RF_ENABLE, LOW); //For V2 //---------------------FIX ME This is specific to p-channel fets, Off is HIGH, On is LOW---------------------
  digitalWrite(RF_ENABLE, HIGH); //For V3  //Fixed
  ask_driver.init();
  serialWriteString("Started Radio\n");

  //---------------------Initialize BMS--------------------------
  twiBegin();                         //FIX ME (twi shouldn't be on by default?)
  pinMode(BMS_INTERRUPT, INPUT);
  attachInterrupt(digitalPinToInterrupt(BMS_INTERRUPT), bmsISR, FALLING);
  pinMode(BMS_OTG, OUTPUT);

  setOTG_CONFIG(true);      //enable boost mode
  setCHG_CONFIG(false);     //Disable charging
  setCONV_RATE(true);       //enable continuous ADC for testing, seems charging needs to be disabled to stop repeated interrupts https://e2e.ti.com/support/power-management/f/196/t/749914
  enableWatchdog(false);    //Disable watchdog
  twiWriteRegister(0x0A, 0x77); //Set BOOST_LIM value to 111 = 2.45A
  setSTAT_DIS(true);
  serialWriteString("Configured bms\n");
  

  initializeTimer2Sleep();
  serialWriteString("Configured Timer2\n");
  
  SMCR|=(1<<SM1)|(1<<SM0); //Set sleep mode control register to PowerSave Mode (Bits SM2 SM1 SM0 = 011 , p38)
  sei();   //Enable global interrupts
  serialWriteString("Enabled interrupts\n");

}

void initializeTimer2Sleep(){
    //Disable timer2 interrupts by zeroing OCIE2A, OCIE2B and TOIE2
    TIMSK2  = 0;
    //Enable asynchronous mode, Only other R/W bit in ASSR is EXCLK which should be 0
    ASSR  = (1<<AS2);
    //set initial counter value
    TCNT2=0;
    //set OCR2B to 128 (approx 4sec), This value should set the frequency of the interrupts
    OCR2B = 0b10000000;
    //OCR2B = 0b00100000;
    //set prescaller 1024
    TCCR2B |= (1<<CS22) | (1<<CS21) | (1<<CS20);
    //wait for registers TCN2UB, OCR2BUB and TCR2BUB to update by checking status is ASSR
    while ( (1<<TCN2UB)&ASSR | (1<<OCR2BUB)&ASSR | (1<<TCR2BUB)&ASSR);
    //clear interrupt flags;  "Output Compare Flag 2 B" and "Timer/Counter2 Overflow Flag"
    TIFR2  = (1<<TOV2) | (1<<OCF2B);
    //enable OCIE2B interrupt to trigger when compare B matches
    TIMSK2  = (1<<OCIE2B);
}

void sleep(){
  initializeTimer2Sleep();
  cli();           //Disable global interrupts because timed sequence follows
  SMCR |= (1<<SE); //Set "Sleep Mode Control Register" Sleep Enable, SE, Bit = 1, p38
  sei();           //Garentees that the next instruction is executed
  sleep_cpu();     //Issue sleep instruction. This cannot be done by setting a register
  //asm volatile("sleep"::); //Assembly version of sleep_cpu();

        //Sleeping until interrupt

  SMCR &= ~(1<<SE); //Disable sleep enable after wakeup
}
ISR(TIMER2_COMPB_vect){    //fires on wakeup
    asm volatile("nop"::);
}

void processISRUpdates(){
  if(requestSwitchToggle){
    toggleSwitch();
    requestSwitchToggle = false;
  }
  if(requestSwitchOn){
    turnOn();
    requestSwitchOn = false;
  }
  if(requestSwitchOff){
    turnOff();
    requestSwitchOff = false;
  }
  if(requestEnableSerial){
    enableSerial();
    requestEnableSerial = false;
  }
  if(requestDisableSerial){
    disableSerial();
    requestDisableSerial = false;
  }
  if(requestBeep){
    beep(numBeeps, 10);
    requestBeep = false;
  }
  if(requestNewPollRate){
    requestNewPollRate = false;
  }
}
void buttonISR(){
    requestSwitchToggle = true;
}
void bmsISR(){
    //serialWriteString("bms!\n");
}

void toggleSwitch(){
  if(switchOn){
    beep(1, 10);
    turnOff();
  }else{
    beep(2, 10);
    turnOn();
  }
}
void turnOn(){
  digitalWrite(BMS_OTG, HIGH); //enable boost mode
  _delay_ms(BMS_OTG_TIME);
  
  servo.attach(SERVO);
  digitalWrite(SERVO_ENABLE, HIGH);
  _delay_ms(15);
  servo.write(ONPOSITION);
  _delay_ms(MOVE_TIME);
  digitalWrite(SERVO_ENABLE, LOW);
  servo.detach();
  switchOn = true;

  digitalWrite(BMS_OTG, LOW);  //disable boost mode
}
void turnOff(){
  digitalWrite(BMS_OTG, HIGH); //enable boost mode
  _delay_ms(BMS_OTG_TIME);
  
  servo.attach(SERVO);
  digitalWrite(SERVO_ENABLE, HIGH);
  _delay_ms(15);
  servo.write(OFFPOSITION);
  _delay_ms(MOVE_TIME);
  digitalWrite(SERVO_ENABLE, LOW);
  servo.detach();
  switchOn = false;

  digitalWrite(BMS_OTG, LOW); //disable boost mode
}
const static char Enable_Serial_Message [] PROGMEM = "Serial enabled\n";
void enableSerial(){
  serialBegin();
  serialWriteProgString(Enable_Serial_Message);
  debugOn = true;
}
const static char Disable_Serial_Message [] PROGMEM = "Goodbye\n";
void disableSerial(){
  serialWriteProgString(Disable_Serial_Message);
  //Serial.end();
  debugOn = false;
}
void beep(int num, int timeMillis){
    for(int i = 0; i < num; i++){
        digitalWrite(BUZZER, HIGH);
        _delay_ms(timeMillis);
        digitalWrite(BUZZER, LOW);
        if (i < num -1){
            _delay_ms(timeMillis*2);
        }
    }
}
void led_blink(int num, int timeMillis){
    for(int i = 0; i < num; i++){
        pinMode(LED, OUTPUT);
        digitalWrite(LED, LOW);
        _delay_ms(timeMillis);
        pinMode(LED, INPUT);
        if (i < num -1){
            _delay_ms(timeMillis*2);
        }
    }
}

//*********************************Conversion functions************************************************//
char outputString[80]; // general output string, 80 bytes

char* longToString(long n){
  ltoa(n, outputString, 10);    // base 10
  return outputString;
}
char* integerToString(int n){   // returns outputString
  itoa(n, outputString, 10);    // itoa is for integers, 10 is for base 10 (could use 2 for binary, 16 for hex)
  return outputString;
}
char* integerToHex(uint32_t n){ // can be any sort of number, long, byte, uint8,16,32 etc
  ltoa(n, outputString, 16);    // base 16 is binary, returns lower case A-F
  return outputString;
}

//*********************************Serial functions************************************************//
unsigned char serialCheckRxComplete(void){
  return( UCSR0A & _BV(RXC0)) ;         // nonzero if serial data is available to read.
}
unsigned char serialCheckTxReady(void){
  return( UCSR0A & _BV(UDRE0) ) ;       // nonzero if transmit register is ready to receive new data.
}
unsigned char serialReadChar(void){
  while (serialCheckRxComplete() == 0); // While data is NOT available to read
  return UDR0;
}
void serialWriteChar(unsigned char DataOut){
  while (serialCheckTxReady() == 0);   // while NOT ready to transmit
  UDR0 = DataOut;
}
void serialWriteString(const char* string){
  const char* ptr = string;
  while(*ptr != 0){
    serialWriteChar(*ptr);
    ptr++;
  }
}
void serialWriteProgString(const char* ptr){
  char c;
  if (!ptr) 
    return;
  while ((c = pgm_read_byte(ptr++)))
    serialWriteChar(c);
}
void serialBegin(){
  UBRR0H = (unsigned char)(CALC_UBRR>>8); //Set baud rate
  UBRR0L = (unsigned char) CALC_UBRR;     //Set baud rate
  UCSR0B = (1<<RXEN0)|(1<<TXEN0);         //Enable receiver and transmitter
  UCSR0C = (3<<UCSZ00);                   // Frame format: 8data, No parity, 1stop bit
  //UCSR0A |= _BV(U2X0);                  //Enable USE_2X (Jared added this)
}

//*********************************RH_ASK wrapper functions****************************************//
void processASKCommands(byte* commands, int len){
  byte* ptr = commands;
  while(*ptr != SLEEP){
    if(*ptr == BEEP){
        ptr++;
        numBeeps = *ptr;
        requestBeep = true;
    }else if(*ptr == SET_POLL_RATE){
        ptr++;
        pollRate = *ptr;
        requestNewPollRate = true;
    }else if(*ptr == SWITCH_ON){
        requestSwitchOn = true;
    }else if(*ptr == SWITCH_OFF){
        requestSwitchOff = true;
    }else if(*ptr == SWITCH_TOGGLE){
        requestSwitchToggle = true;
    }else if(*ptr == ENABLE_SERIAL){
        requestEnableSerial = true;
    }else if(*ptr == DISABLE_SERIAL){
        requestDisableSerial = true;
    }else if(*ptr == SLEEP){
        return;
    }
    ptr++;
  }
}
byte receiveASKByte(){
    ask_driver.init();
    uint8_t buf[1] = {0};
    uint8_t buflen = sizeof(buf);
    while(!ask_driver.recv(buf, &buflen));
    return(buf[0]); 
}
void receiveASKBytes(byte* buf, byte* len){
    ask_driver.init();
    while(!ask_driver.recv(buf, len));
}

void transmitASKByte(byte data){
    ask_driver.init();
    ask_driver.send(&data, 1);
    ask_driver.waitPacketSent();
}
void transmitASKBytes(byte* data, int len){
    ask_driver.init();
    ask_driver.send(data, len);
    ask_driver.waitPacketSent();   
}
byte checkASKByte(){
    uint8_t buf[1];
    uint8_t buflen = sizeof(buf);
    if(ask_driver.recv(buf, &buflen)){
        return(buf[0]); 
    }else{
        return NULL;
    }
}

//*********************************twi functions****************************************//
//https://github.com/knightshrub/I2C-master-lib/blob/master/i2c_master.c
uint8_t twiReadRegister(uint8_t address){
    twiStart();
    twiWrite(BMS_WRITE_ADDR);     //Select BMS in write mode
    twiWrite(address);            //Select register
    twiStart();
    twiWrite(BMS_READ_ADDR);      //Select BMS in read mode
    uint8_t data = twiReadNACK(); //Send NACK right away because we are only reading one byte
    twiStop();
    return data;
}
void twiWriteRegister(uint8_t address, uint8_t data){
    twiStart();
    twiWrite(BMS_WRITE_ADDR);  //Select BMS in write mode
    twiWrite(address);         //Select register
    twiWrite(data);            //Write data 
    twiStop();
}
void twiBegin(){
    //SCL_FREQ = F_CPU / (16+2*TWBR*PreScale), if we want SCL 100kHz  then TWSR*TWBR = 32
    PRR &= ~(1<<PRTWI); //Enable TWI clock from sleep
    TWSR = 0x00;        //Don't need prescaler so set to 1
    TWBR = 0x20;        //Set TWBR=32(dec), should set SCL to 100kHz
    TWCR = (1<<TWEN);   //enable TWI
}
void twiEnd(){
    TWCR &= ~(1<<TWEN); //Disable TWI
    PRR |= (1<<PRTWI);  //Disable TWI clock for sleep
}
uint8_t twiStart(){
    TWCR = 0;                                //Reset TWI control register
    TWCR = (1<<TWINT)|(1<<TWSTA)|(1<<TWEN);  //TWINT will be set (written to 0) when start is actually sent
    //while ( TWCR & (1<<TWINT) != 0);       //Wait until TWINT = 0
    while( !(TWCR & (1<<TWINT)) );           //Wait for end of transmission
    if((TWSR & 0xF8) != TW_START){
      return 1; 
    }
    return 0;
}
void twiStop(){
    TWCR = (1<<TWINT)|(1<<TWSTO)|(1<<TWEN);
}
uint8_t twiWrite(uint8_t u8data){
    TWDR = u8data;
    TWCR = (1<<TWINT)|(1<<TWEN);
    //while ( TWCR & (1<<TWINT) != 0); //Wait until TWINT = 0
    while( !(TWCR & (1<<TWINT)) );     // wait for end of transmission
  
    if( (TWSR & 0xF8) != TW_MT_DATA_ACK ){
      return 1; 
    }
    return 0;
}
uint8_t twiReadACK(){ 
    TWCR = (1<<TWINT)|(1<<TWEN)|(1<<TWEA);
    //while ( TWCR & (1<<TWINT) != 0);         //Wait until TWINT = 0
    while( !(TWCR & (1<<TWINT)) ); // wait for end of transmission
    return TWDR;
}
uint8_t twiReadNACK(){
    TWCR = (1<<TWINT)|(1<<TWEN);
    //while ( TWCR & (1<<TWINT) != 0);         //Wait until TWINT = 0
    while( !(TWCR & (1<<TWINT)) ); // wait for end of transmission
    return TWDR;
}
uint8_t twiGetStatus(){
    uint8_t statusByte;
    statusByte = TWSR & 0xF8; //mask status
    return statusByte;
}
void twiWriteRegisterBit(byte address, int pos, bool value){
  byte currentData = twiReadRegister(address);         //Read the current state
  currentData = bitWrite(currentData, pos, value);     //Change the specified bit
  twiWriteRegister(address, currentData);              //Write the changes
}

//*********************************BMS functions****************************************//
void setCONV_RATE(bool value){ //Configure continuous ADC updates = TRUE, one shot mode = FALSE
  twiWriteRegisterBit(0x02, 6, value);
}
void setOTG_CONFIG(bool value){
  twiWriteRegisterBit(0x03, 5, value);
}
void setCHG_CONFIG(bool value){
  twiWriteRegisterBit(0x03, 4, value);
}
void setSTAT_DIS(bool value){
  twiWriteRegisterBit(0x07, 6, value);
}
void setWD_RST(bool value){
  twiWriteRegisterBit(0x03, 6, value);
}
void enableWatchdog(bool value){ //00 for disabled, 01 for 40s, 10 for 80s and 11 for 160s
  int bit5;
  int bit4;
  if(value){ bit5 = 0; bit4 = 1; }
  else{      bit5 = 0; bit4 = 0; }
  byte currentData = twiReadRegister(0x07);         
  currentData = bitWrite(currentData, 5, bit5);  
  currentData = bitWrite(currentData, 4, bit4); 
  twiWriteRegister(0x07, currentData);
}

//**********************************Print methods**********************************************//
void printAllREG(){
  
  serialWriteChar('\n');
  for(int i = 0; i < 50; i++) serialWriteChar('*');
  serialWriteChar('\n');

  printREGBinary(0x00);
  printREGBinary(0x01);
  printREGBinary(0x02);
  printREGBinary(0x03);
  printREGBinary(0x04);
  printREGBinary(0x05);
  printREGBinary(0x06);
  printREGBinary(0x07);
  printREGBinary(0x08);
  printREGBinary(0x09);
  printREGBinary(0x0A);
  serialWriteChar('\n');

  //Registers 0B to 14 are primarily read only,
  printREG0B();
  serialWriteChar('\n');
  printREG0C();
  serialWriteChar('\n');
  printREG0D();
  serialWriteChar('\n');
  printREG0E();
  serialWriteChar('\n');
  printREG0F();
  printREG10();
  printREG11();
  printREG12();
  serialWriteChar('\n');
  printREG13();
  serialWriteChar('\n');
  printREG14();

  serialWriteChar('\n');
  for(int i = 0; i < 50; i++) serialWriteChar('*');
  serialWriteChar('\n');
}

const static char Register_[] PROGMEM = "Register ";
void printREGBinary(byte address){
  byte data = twiReadRegister(address);
  byte mask = 0b10000000;
  
  serialWriteProgString(Register_);
  serialWriteString("0x");
  serialWriteString(integerToHex(address));
  serialWriteString(": ");
  
  for(int i = 0; i<8; i++){
    if(((mask >> i) & data) == (mask>>i)){
      serialWriteChar('1');
    }else{
      serialWriteChar('0');
    }
  }
  serialWriteChar('\n');
}

const static char Charger_Status_Message [] PROGMEM = "Charger status: ";
const static char No_Charger_Message [] PROGMEM = "No charger";
const static char USB_Host_SDP_Message [] PROGMEM = "USB Host SDP";
const static char USB_CDP_Message [] PROGMEM = "USB CDP (1.5A)";
const static char USB_DCP_Message [] PROGMEM = "USB DCP (3.25A)";
const static char MaxCharge_Message [] PROGMEM = "Adjustable High Voltage DCP (MaxCharge) (1.5A)";
const static char Unknown_Adapter_Message [] PROGMEM = "Unknown Adapter (500mA)";
const static char Non_Standard_Adapter_Message [] PROGMEM = "Non-Standard Adapter (1A/2A/2.1A/2.4A)";
const static char OTG_Mode_Message [] PROGMEM = "OTG mode";

const static char Charging_Mode_Message [] PROGMEM = "Charging mode: ";
const static char Not_Charging_Message [] PROGMEM = "Not Charging";
const static char Pre_Charging_Message [] PROGMEM = "Pre-charge";
const static char Fast_Charging_Message [] PROGMEM = "Fast Charging";
const static char Charge_Termination_Done_Message [] PROGMEM = "Charge Termination Done";

const static char Power_Status_Message [] PROGMEM = "Power status: ";
const static char Error_Message [] PROGMEM = "Error";
const static char Good_Message [] PROGMEM = "Good";

const static char VSYS_Message [] PROGMEM = "VSYS Regulation Status: ";
const static char No_VSYS_Reg_Message [] PROGMEM = "NOT in VSYSMIN regulation (BAT > VSYSMIN)";
const static char VSYS_Good_Message [] PROGMEM = "Good (BAT < VSYSMIN)";

void printREG0B(){
  byte data = twiReadRegister(0x0B);
  serialWriteProgString(Charger_Status_Message);   //print charger information
  
  byte charger = data >> 5;
  if      (charger == 0) serialWriteProgString(No_Charger_Message);
  else if (charger == 1) serialWriteProgString(USB_Host_SDP_Message);
  else if (charger == 2) serialWriteProgString(USB_CDP_Message);
  else if (charger == 3) serialWriteProgString(USB_DCP_Message);
  else if (charger == 4) serialWriteProgString(MaxCharge_Message);
  else if (charger == 5) serialWriteProgString(Unknown_Adapter_Message);
  else if (charger == 6) serialWriteProgString(Non_Standard_Adapter_Message);
  else if (charger == 7) serialWriteProgString(OTG_Mode_Message);
  serialWriteChar('\n');

  //print charging status
  serialWriteProgString(Charging_Mode_Message);
  byte chargeStatus = data << 3;
  chargeStatus = chargeStatus >> 6;
  if      (chargeStatus == 0) serialWriteProgString(Not_Charging_Message);
  else if (chargeStatus == 1) serialWriteProgString(Pre_Charging_Message);
  else if (chargeStatus == 2) serialWriteProgString(Fast_Charging_Message);
  else if (chargeStatus == 3) serialWriteProgString(Charge_Termination_Done_Message);
  serialWriteChar('\n');

  //print power good
  serialWriteProgString(Power_Status_Message);
  byte powerStatus = data << 4;
  powerStatus = powerStatus >> 7;
  if      (powerStatus == 0) serialWriteProgString(Error_Message);
  else if (powerStatus == 1) serialWriteProgString(Good_Message);
  serialWriteChar('\n');

  //print power good
  serialWriteProgString(VSYS_Message);
  byte vsysStatus = data << 7;
  vsysStatus = vsysStatus >> 7;
  if      (powerStatus == 0) serialWriteProgString(No_VSYS_Reg_Message);
  else if (powerStatus == 1) serialWriteProgString(VSYS_Good_Message);
  serialWriteChar('\n');
}

const static char Watchdog_Message [] PROGMEM = "Watchdog status: ";
const static char Normal_Message [] PROGMEM = "Normal";
const static char Timer_Expired_Message [] PROGMEM = "Timer expired";

const static char Boost_Status_Message [] PROGMEM = "Boost status: ";
const static char VBUS_Overloaded_Message [] PROGMEM = "VBUS overloaded in OTG, or VBUS OVP, or battery is too low in boost mode";

const static char Input_Fault_Message [] PROGMEM = "Input fault";
const static char Thermal_Shutdown_Message [] PROGMEM = "Thermal shutdown";
const static char Charger_Safety_Message [] PROGMEM = "Charge safety timer expiration";

const static char Battery_Status_Message [] PROGMEM = "Battery status: ";
const static char Battery_Overvoltage_Message [] PROGMEM = "Battery over-voltage";

const static char NTC_Status_Message [] PROGMEM = "NTC status: ";
const static char TS_Warm_Message [] PROGMEM = "TS Warm";
const static char TS_Cool_Message [] PROGMEM = "TS Cool";
const static char TS_Cold_Message [] PROGMEM = "TS Cold";
const static char TS_Hot_Message [] PROGMEM = "TS Hot";
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

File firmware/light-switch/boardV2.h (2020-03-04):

#ifdef F_CPU
#undef F_CPU
#define F_CPU 8000000UL
#endif

#define BUTTON 3         //PD3, INT1
#define LED 7            //PD7
#define BUZZER 10        //PB2
#define RF_ENABLE 4      //PD4
#define TRANSMITTER 5    //PD5
#define RECEIVER 6       //PD6
#define VAR_RESISTOR A7  //PE3, ADC7

//Serial Constants
#define BaudRate 38400
#define CALC_UBRR (F_CPU / (16 * BaudRate)) - 1  //Disable 2x mode
//#define CALC_UBRR (F_CPU / (8 * BaudRate)) - 1  //Requires 2x mode
//#define CALC_UBRR 12  //38.4k

//BMS Constants
#define BMS_INTERRUPT 2  //PD2, INT0
#define BMS_OTG A3       //PC3
#define BMS_CE A2        //PC2
#define BMS_QON A1       //PC1
//I2C Slave Address: 6AH (1101010B + R/W) (bq25890)
//For read:  0b11010101  -> 0xD5
//For write: 0b11010100  -> 0xD4
#define BMS_READ_ADDR 0xD5
#define BMS_WRITE_ADDR 0xD4
#define BMS_OTG_TIME 100 //Turn-on time

//Servo Constants
#define SERVO 9          //PB1
#define SERVO_ENABLE 8   //PB0
#define ONPOSITION 70    //Confirmed 75
#define OFFPOSITION 125  //115
#define MOVE_TIME 500

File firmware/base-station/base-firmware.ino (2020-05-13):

#include <IotWebConf.h>
#include <FS.h>
#include <MQTT.h>
#include <RH_ASK.h>
#include "constants.h"

//#define F_CPU 8000000UL

//RH_ASK module PINS
#define TRANSMITTER 2
#define RECEIVER 0

//RH_ASK driver(2000, RECEIVER, TRANSMITTER, -1, false);
RH_ASK ask_driver(500, RECEIVER, TRANSMITTER, -1, false);

volatile long transmitTimer = 0;

// Initial name of the Device. Used e.g. as SSID of the own Access Point.
const char deviceName[] = "jSwitch";

// Initial password to connect to the Thing, when it creates an own Access Point.
const char wifiInitialApPassword[] = "password";

#define STRING_LEN 128
#define NUMBER_LEN 32

// When CONFIG_PIN is pulled to ground on startup, initial password is used to create the AP
#define CONFIG_PIN 3 //GPIO3 is also RX pin
// -- Status indicator pin. First it will light up (kept LOW), on Wifi connection it will blink, when connected to the Wifi it will turn off (kept HIGH).
#define STATUS_PIN 1 //GPIO1 is also TX pin

// Configuration specific key. The value should be modified if config structure was changed.
#define CONFIG_VERSION "v1.7"

// Callback method declarations.
void configSaved();
boolean formValidator();

DNSServer dnsServer;
WebServer server(80);
WiFiClient net;
MQTTClient client;

char stringParamValue[STRING_LEN];
char intParamValue[NUMBER_LEN];

IotWebConf *iotWebConf; //Can't construct until after we've switched the pins to GPIO
IotWebConfSeparator *separator1;
IotWebConfParameter *userIDParam;
IotWebConfSeparator *separator2;
IotWebConfParameter *pollingRateParam;

bool requestSwitchOn = false;
bool requestSwitchOff = false;
bool requestSwitchToggle = false;
bool requestEnableSerial = false;
bool requestDisableSerial = false;

bool requestBeep = false;
byte numBeeps = 0;
bool requestNewPollRate = false;
byte pollRate = 0;

void setup()
{ 
  pinMode(CONFIG_PIN, FUNCTION_3); //Call Function0 to restore back to orginal state
  pinMode(STATUS_PIN, FUNCTION_3);

  iotWebConf = new IotWebConf(deviceName, &dnsServer, &server, wifiInitialApPassword, CONFIG_VERSION);
  separator1 = new IotWebConfSeparator("User Settings");
  userIDParam = new IotWebConfParameter("User ID", "stringParam", stringParamValue, STRING_LEN, "text", "e.g. jaredpoole");
  separator2 = new IotWebConfSeparator("Device Settings");
  pollingRateParam = new IotWebConfParameter("Polling rate", "intParam", intParamValue, NUMBER_LEN, "number", "0-8sec", NULL, "min='0' max='8' step='1'");

  
  //Serial.begin(115200);
  //Serial.println();
  //Serial.println("Booting up...");

  if(!SPIFFS.begin()){
    //Serial.println("An Error has occurred while mounting SPIFFS");
    return;
  }
  iotWebConf->setStatusPin(STATUS_PIN);
  iotWebConf->setConfigPin(CONFIG_PIN);
  
  iotWebConf->addParameter(separator1);
  iotWebConf->addParameter(userIDParam);
  iotWebConf->addParameter(separator2);
  iotWebConf->addParameter(pollingRateParam);
  iotWebConf->setConfigSavedCallback(&configSaved);
  iotWebConf->setFormValidator(&formValidator);
  iotWebConf->getApTimeoutParameter()->visible = true;
  
  iotWebConf->init();

  server.on("/", handleRoot);
  server.on("/config", []{ iotWebConf->handleConfig(); });
  server.onNotFound([](){ handleFileRead(); });
  //server.onNotFound([](){ iotWebConf->handleNotFound(); });

  //RH_ASK
  if (!ask_driver.init()){
    //Serial.println("RH_ASK init failed");
  }

  //MQTT
  // Note: Local domain names (e.g. "Computer.local" on OSX) are not supported by Arduino.
  // You need to set the IP address directly.
  client.begin("jservices.site", net);
  client.onMessage(messageReceived);
  //connect();
  
  //Serial.println("Ready.");
}

void loop()
{
  //RH_ASK
  processRF();
  
  //WebServer
  iotWebConf->doLoop();

  
  //MQTT
  if (WiFi.status() == WL_CONNECTED){
    if (!client.connected()) { 
      client.connect(deviceName); 
      client.subscribe("light-switch/state");
    }
    client.loop();
    delay(10);  //fixes some issues with WiFi stability
  }

  //Refreshes external led
  updateStatusLED();
  
}


// Handle web requests to "/" path.
void handleRoot(){ 
  if (iotWebConf->handleCaptivePortal()){  // Let IotWebConf test and handle captive portal requests.   
    return;                               //Captive portal request were already served.
  }
  File file = SPIFFS.open("/root.html", "r");
  server.streamFile(file, "text/html");
  file.close();
}

String getContentType(String filename){
  if(filename.endsWith(".htm"))       return "text/html";
  else if(filename.endsWith(".html")) return "text/html";
  else if(filename.endsWith(".css"))  return "text/css";
  else if(filename.endsWith(".js"))   return "application/javascript";
  else if(filename.endsWith(".png"))  return "image/png";
  else if(filename.endsWith(".gif"))  return "image/gif";
  else if(filename.endsWith(".jpg"))  return "image/jpeg";
  else if(filename.endsWith(".ico"))  return "image/x-icon";
  else if(filename.endsWith(".xml"))  return "text/xml";
  else if(filename.endsWith(".pdf"))  return "application/x-pdf";
  else if(filename.endsWith(".zip"))  return "application/x-zip";
  else if(filename.endsWith(".gz"))   return "application/x-gzip";
  return "text/plain";
}

//Serve the right file to the client (if it exists)
bool handleFileRead() { 
  if (iotWebConf->handleCaptivePortal()){
    return true;
  }
  String path = server.uri();
  Serial.println("handleFileRead: " + path);
  String contentType;
  if (path.endsWith("/") || !SPIFFS.exists(path) ){   // If a folder is requested or SPIFFS can't find the file, send the 404 file
    path = "/404.html";     
    contentType = "text/html";
    Serial.println("\tFile Not Found");
  }else{
    contentType = getContentType(path);               // Get the MIME type
  }
  File file = SPIFFS.open(path, "r");                 // Open it
  size_t sent = server.streamFile(file, contentType); // And send it to the client
  file.close();                                       // Then close the file again
  return true;
}

void configSaved(){
  Serial.println("Configuration was updated.");
}

boolean formValidator(){
  Serial.println("Validating form.");
  boolean valid = true;

  int l = server.arg(userIDParam->getId()).length();
  if (l < 1){
    userIDParam->errorMessage = "User ID cannot be empty";
    valid = false;
  }
  return valid;
}
void messageReceived(String &topic, String &payload) {
  //Serial.println("incoming: " + topic + " - " + payload);
  if(payload == "on"){
    requestSwitchOn = true;
    //Serial.println("Turning on");
  }else if(payload == "off"){
    requestSwitchOff = true;
    //Serial.println("Turning off");
  }
}

void updateStatusLED(){
  if(requestSwitchOn || requestSwitchOff || requestSwitchToggle || requestEnableSerial || requestDisableSerial || requestBeep || requestNewPollRate){
    iotWebConf->blink(200, 50);
  }else{
    iotWebConf->stopCustomBlink();
  }
}

void transmitASKByte(byte data){
    ask_driver.send(&data, 1);
    ask_driver.waitPacketSent();   
}
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

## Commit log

2019-09-07 Added pin definitions
2019-10-16 Added i2c Control
2019-11-16 power test
2019-12-23 Updated power management
2019-12-25 Fixed timer2 demo
2022-12-30 Added base station docs (#1)
    [BOM.csv]
2022-12-30 Daughterboard docs (#2)
    [assembly.SLDASM, button.SLDPRT, button.STL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]
2022-12-31 Added Mechanical Docs (#5)
    [18650_battery.SLDPRT, 1s4p_battery_inner_tab.SLDPRT, 1s4p_battery_outer_tab.SLDPRT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]
